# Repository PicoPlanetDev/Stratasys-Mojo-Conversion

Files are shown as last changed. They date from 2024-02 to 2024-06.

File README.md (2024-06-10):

# Stratasys Mojo Retrofit

Stratasys has ended support for their Mojo 3D printers, and you can no longer purchase parts or filament for them.
This project aims to retrofit them with off-the-shelf parts to extend their lifespan.

## Parts

Here is an example parts list that may be used for this conversion. This assumes that you repurpose the
old printer's ATX power supply and CoreXY mechanics. Minmimal irreversible changes are made to the machine,
although that doesn't really matter at this point!

I converted two printers at once for $300, a slight cost savings due to higher quantity of GT2 pulleys resulting in a lower individual price, as well as the endstops comkng in packages of six.

| **Item** | **URL** | **Price** | **Quantity** | **Total Cost** |
|:---:|:---:|:---:|:---:|:---:|
| Chimera hotend | <https://www.amazon.com/dp/B08BKMM1R7/> | $20 | 1 | $20 |
| Extruder | <https://www.amazon.com/dp/B0BZD8JMPR/> | $9 | 2 | $18 |
| Control board | <https://www.amazon.com/dp/B08PCX6TM7/> | $42 | 1 | $42 |
| Endstops | <https://www.amazon.com/dp/B07PCN6T6F/> | $11 | 1 | $11 |
| PTFE tubing | <https://www.amazon.com/dp/B01CUPV90M/> | $8 | 1 | $8 |
| Stepper motors | <https://www.amazon.com/dp/B0817TS61F/> | $38 | 1 | $38 |
| LCD display | <https://www.amazon.com/dp/B08HLSCHVL/> | $12 | 1 | $12 |
| GT2 timing belt pulleys | <https://www.amazon.com/dp/B07BT6N12L/> | $8 | 1 | $8 |
| 4010 fan | <https://www.amazon.com/dp/B0B1N6NSGM/> | $9 | 1 | $9 |
| **Total** | | | | **$166** |

You'll also need some assorted M3 screws. I use them standard across all of my designs now and just bought a little box of a few size off of Amazon. Your local hardware store might be better though!

### 3D Printed Parts

In the `cad/` subdirectory, I have included designs in both Fusion 360 and STEP formats for you to customize and export. STLs and potentially Printables links coming soon!

| **Part** | **Quantity** |
|:---:|:---:|
| Chimera Mount | 1 |
| Left Extruder Mount  | 1 |
| Right Extruder Mount | 1 |
| Stepper Mount | 3 |
| ~~Z Endstop Mount~~  | ~~1~~ |

Note that the Z Endstop Mount design is currently **not** suitable for the conversion. It doesn't allow the bed to move up enough to reach the hotend. Future revision will correct this, however,
I just use hot glue and software offsets in the meantime.

#### Buildplate

[@mebillica](https://github.com/mebillica) has improved the accuracy of my build plate design used in the PrusaSlicer model preview to the point that it can be printed and used in the abscence
of OEM buildplates, an increasingly prevalent issue with Stratasys Mojo machines after their discontinuation.

[Here's a link](https://www.thingiverse.com/thing:6648382) to his model on Thingiverse, which also includes the Fusion source if you need to make further modifications. The Fusion design and STL file
are also mirrored in this repo, in the `cad/Fusion/Build Plate` and `PrusaSlicer/buildplate` directories, respectively. If you'd prefer the Printables download, that is [available as well](https://www.printables.com/model/901716-stratasys-mojo-build-plate).

Stratasys OEM buildplates are made of some some sort of ABS plastic so that their ABS filament fuses to them. This makes them non-reuseable unless you cover first with transfer tape (and a glue stick).
However, if you're looking to print PLA using a machine retrofitted according to this guide, you may have success printing these plates out of other materials.

PrusaSlicer should now show this new buildplate design in the Plater tab when setting up your prints, giving you an even better idea of where your model lands relative to the 5" grid as well
as locking mechanism.

### Laser Cut Parts

If you have access to a laser cutter, it can be really useful for quickly making the following parts out of acrylic:

- LCD frontplate
- LCD backplate
- Control board backplate
- Control board standoffs
- Control board fan mount

However, a laser cutter is not required and these could easily be made manually with careful marking, a drill press, and a jigsaw, or 3D printed if you're willing to run a relatively long print.

These design files are not yet included.

## Assembly

### Removing original hardware

I'd suggest using a drill with the clutch limited to about 5 (attached to an appropriately sized socket head) to remove all of the screws. Probably you'll want a magnetic screw dish as well.

1. Remove the metal backplate after unscrewing all of the screws marked in red image **red** in the below image
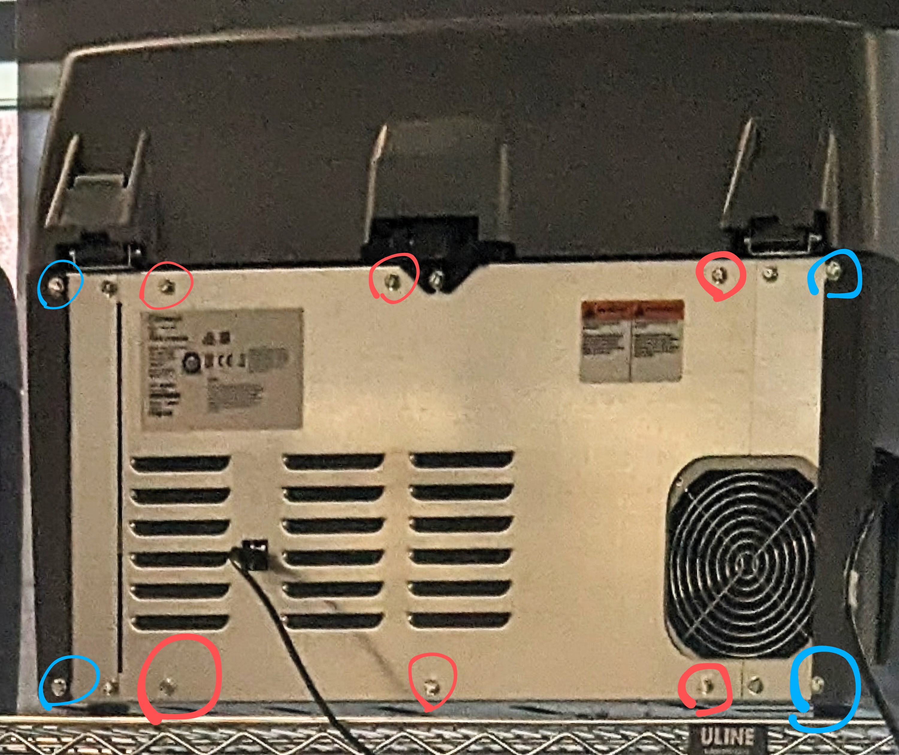
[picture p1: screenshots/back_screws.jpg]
Back screws to remove

1. Remove the two side panels after unscrewing all of the screws marked in blue image **blue** in the above image
2. Unplug every connector from the original I/O board, including the power cables and all ribbon cables
3. Unscrew each screw keeping the I/O board in place, then remove it
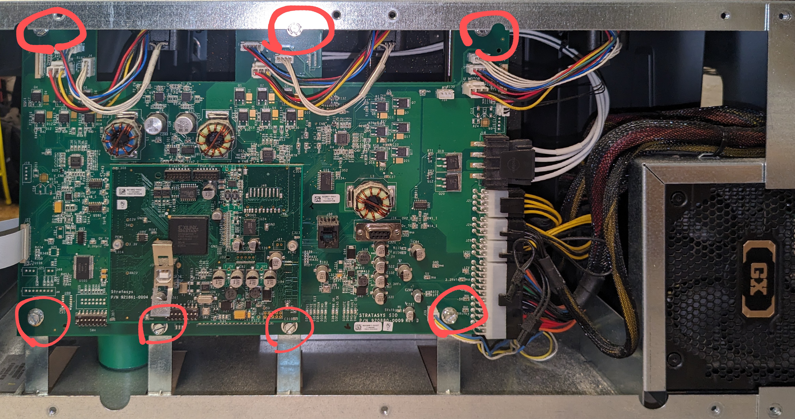
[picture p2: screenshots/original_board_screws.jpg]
I/O board screws to remove

1. *Carefully* bend the metal tabs previously holding the I/o board in place out of the way. Ideally all should be in a flush position, save for the small bump where they are attached.
2. Unscrew and remove both filament buckets. There's four obvious screws on the top, but also one hidden one that I had to use a screwdriver plus shaft extension on:
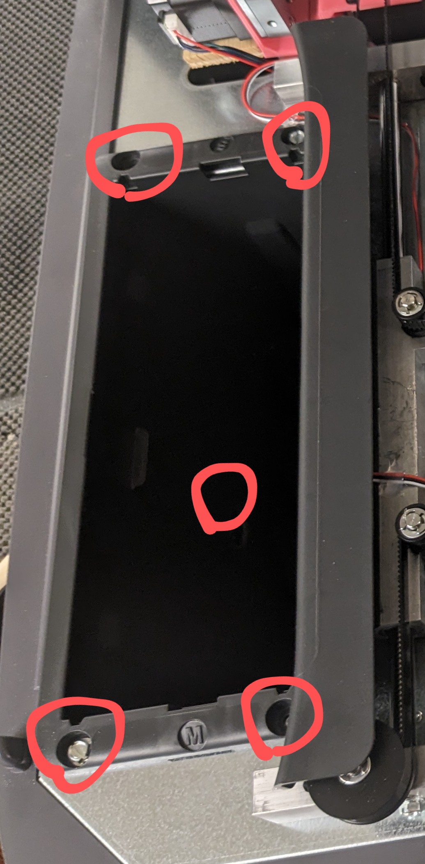
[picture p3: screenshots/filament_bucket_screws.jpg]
Filament bucket screws to remove

1. Remove the original hotend carrier. This takes some work, and many screws that I don't (yet) have documentation photos for. This is a general guide and it took at least an hour of messing with it the first time I did it.
   1. First, try unscrewing the PCB on the back
   2. Remove the belts from their tensioning system and unscrew the back from its slider
   3. Remove the clip holding the front on, and I think you can take out the entire assembly
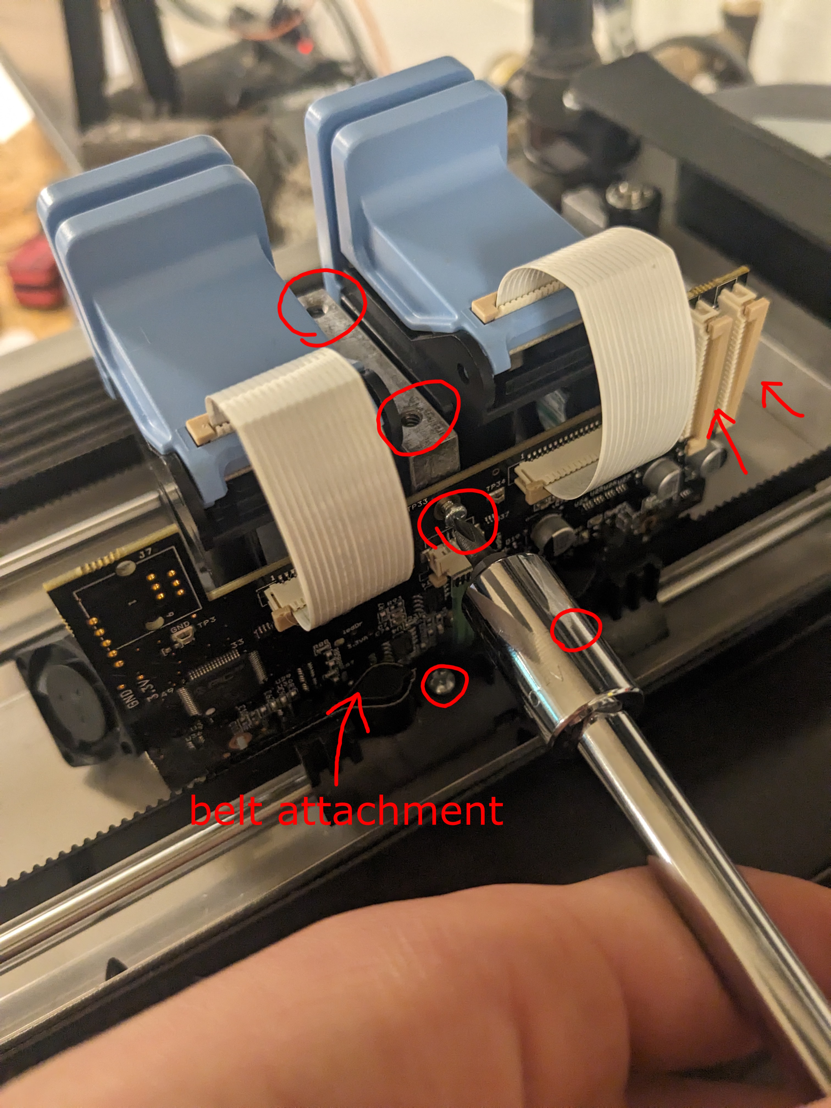
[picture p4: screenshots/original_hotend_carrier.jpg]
Hotend carrier


### Installing new hardware

In lieu of a full assembly guide (right now), I'll just add some notes.

- If you're not using a heated bed, just power the control board off of the power supply's PCIe power
  - Snip off the last couple of inches of the header
  - Twist together the three yellow wires, then separately twist together the three black wires
  - Maybe put a blob of solder on the twists to keep them in place while inserting into the control board's screw terminals
- When viewing the printer **from the back**, the left motor should be plugged into the **X** connector and the right motor into the **Y** connector
- You'll need to drill some ~1" holes through the side panels and filament buckets to accomodate a dowel rod for the filament spool
  - Alternatively, for a no-damage installation, print first one of the filament spool holder designs that uses bearings and rollers to support the filament and allow it to spin freely
- Your Y axis endstop should be on the right side when viewed **from the front** or left side when viewed **from the back**, a couple of inches towards the back away from the front block. You can identify the right position by pushing the Y axis all the way forward, then placing the endstop in a position so it is well depressed.
  - Depending on your printer, you may be able to screw down one or both of the endstop's mounting holes. I used a 1/8" drill bit and, after marking the position, drilled through the metal with a shop vac for cleanup only
- All endstops need some insulation on the bottom to prevent shorts. Either heatshrink the whole thing, which would hide the LED :(, or, as I did, liberally apply hot glue to the bottom
  - Then, for all of the endstops, use more hot glue to affix in place as necessary
- The Z axis endstop now has a custom mount consisting of a U-shaped bracket that slides over the Z axis block and a separate plate that the endstop mounts to and slides up and down on to adjust the zero offset. The U-shaped bracket probably should be glued down once everything's all set
- Don't forget that ATX computer power supplies require their PS_On pin (#6 on a 24-pin connector) to be jumped to ground to activate them. As I have not implemented power supply control, please use a short piece of wire to connect PS_on (also denoted by the green wire) to any black ground wire.

## Firmware

The firmware for the prototype single extruder system is based on Marlin 2.0.9.7 LTS which is not recommended for use with "modern" boards. For that machine, I was reusing an old mega2560 MKS Base v1.4 control board, but I could have used a newer Marlin version, and I'd suggest you update the config to do that.

The dual nozzle version is currently based on Marlin 2.1-bugfix as of 5 April 2024, but I intend to upgrade it to 2.1.3 when that becomes available. I'm using the MKS Eagle (basically Robin Nano with builtin drivers) for the production version, so the config files and binary reflect that.

### Build and Upload

As this was my first time dealing with a 32-bit control board, the process for uploading firmware was initially foreign to me. *Here's the process I found to be best for quick iteration:*

1. Clone or download [makerbase-mks/MKS-EAGLE](https://github.com/makerbase-mks/MKS-EAGLE)
2. Clone or download this repository (for easy access to the Marlin configuration files)
3. Download and extract the appropriate version of Marlin from [this page](https://marlinfw.org/meta/download/)
4. Copy the configuration files from the appropriate subfolder of the `firmware` folder in this repository, and paste them in the Marlin subfolder that you extracted. You should see in the same directory the folders `lib` and `src` in addition to the file `Marlin.ino` if you're in the right place.
5. Install [Visual Studio Code](https://code.visualstudio.com/#alt-downloads) using the download link for your platform
6. Set up Auto Build Marlin according to [these instructions](https://marlinfw.org/docs/basics/auto_build_marlin.html)
7. Customize the example configuration
8. Build using the Build button in the Auto Build Marlin window
9. Find your `mks_eagle.bin` output file. It should be located in `../.pio' folder (one level outside of the Marlin folder)
10. Copy `mks_eagle.bin` to the `DFU-upload` folder downloaded from the MKS-EAGLE repository. Overwrite the `mks_eagle.bin` that's already there.
11. Ensure that your control board is entirely unpowered, then move the board's power jumper (near the USB Type B port and microSD slot) to USB power (on)
12. Press and hold the `BOOT0` button on the board, then plug it in to your computer using the included cable. Once it's plugged in, release the button.
13. Download and run the latest version of [Zadig](https://zadig.akeo.ie/), which will help install necessary USB drivers.
14. Once Zadig is running, click `Options` then `List All Devices` then select from the top dropdown a device like `STM Bootloader`
15. Set the driver in the right-side combobox to WinUSB, and then click `Replace Driver`. This process can surprisingly take a few minutes to complete.
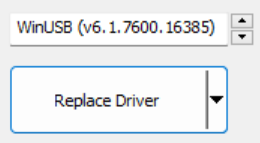
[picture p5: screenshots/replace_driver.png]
Screenshot of Zadig window for driver replacement

16. In the `MKS-EAGLE/DFU-upload` folder, run `DFU-Upload-firmware.bat`
17. Once flashing is complete, unplug the board and change the power jumper back to off (so no USB power)
18. Turn on your power supply and test the firmware!

## Slicer

I selected PrusaSlicer for its robustness and ease of customization, however, I believe that derivatives such as SuperSlicer or OrcaSlicer will also work.
Or, if you prefer Cura, as I do for my other machines, the configuration should be easy enough to replicate.

1. Install [PrusaSlicer](https://www.prusa3d.com/en/page/prusaslicer_424/).
2. Copy the PrusaSlicer folder from this repository
3. Navigate to `C:/Users/YOUR_USERNAME/AppData/Roaming` in your file explorer. You can do this easily by typing in the directory bar `%APPDATA%` and pressing <kbd>Enter</kbd>.
4. Paste the PrusaSlicer folder, and select *Replace the file in the destination* if prompted. This will install the  filament settings, print settings, and printer settings I have tuned for the Stratasys Mojo conversion.
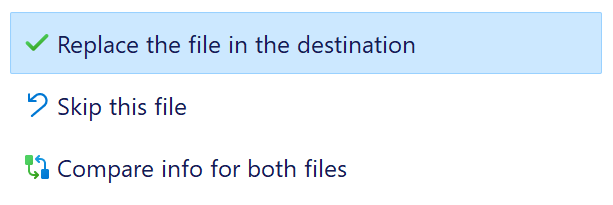
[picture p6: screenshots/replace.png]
Replace file dialog

5. Open PrusaSlicer and navigate to *Printer Settings*.
6. Ensure that Expert mode is selected by pressing the button in the top right.
7. Navigate to *General* > *Bed Shape*.
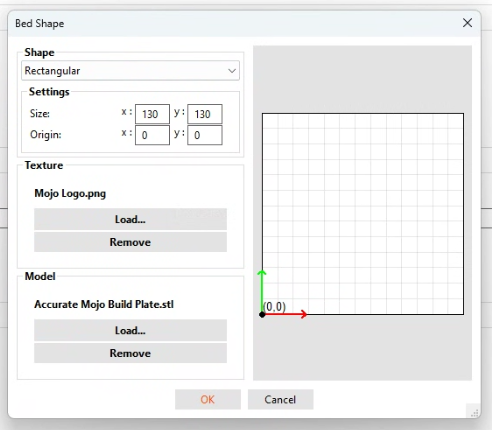
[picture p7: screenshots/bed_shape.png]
Bed Shape dialog

1. Load the `Mojo Logo.png` file from the `PrusaSlicer/buildplate` folder you copied as the bed texture.
2. Load the `Accurate Mojo Build Plate.stl` file `PrusaSlicer/buildplate` folder you copied as the bed model.

## Usage Instructions

I created a guide with instructions for a novice user to prepare a model for printing on one of these converted machines.
That document is available here: [Stratasys Mojo Instructions](https://docs.google.com/document/d/1dcEKFhcxA-QaMBZmRmVCBlgQjbNByx9ydnzFRXKonwo/edit?usp=sharing)

## TODO

- [x] Update to 2.1-bugfix
- [x] Implement M16 in print profile to ensure that the right profile (dual vs single extruder) was used
- [ ] ~~Figure out feasibility of ATX power supply enable / disable and standby power~~
- [ ] Consider MPC temperature instead of PID
- [ ] Consider S-Curve acceleration
- [ ] Consider nozzle clean
- [ ] Enable linear advance
- [ ] ~~Consider sensorless homing~~
- [ ] Create X axis endstop mount
- [x] Create both extruder mounts

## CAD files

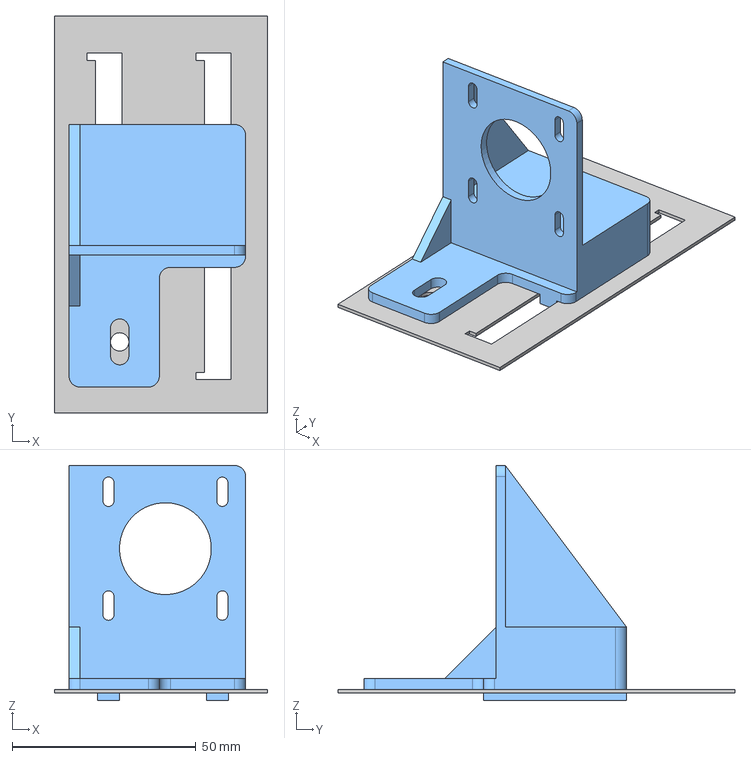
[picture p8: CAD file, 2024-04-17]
cad/STEP/Right Extruder Mount v5.step
58.1 x 108.0 x 64.0 mm
Metal Base
Mounting Plate

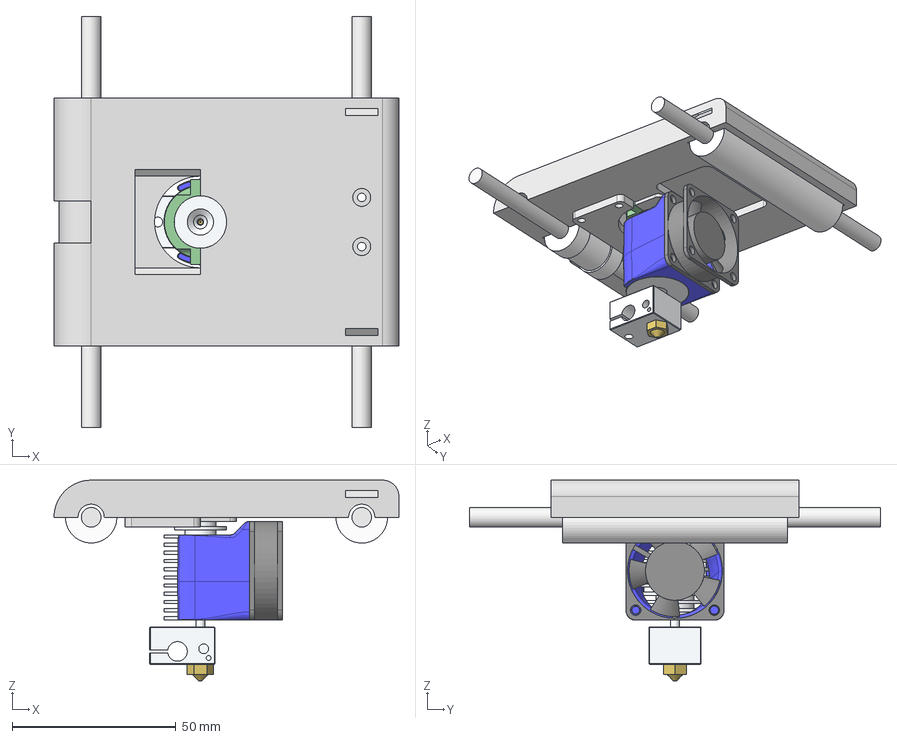
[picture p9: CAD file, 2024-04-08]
cad/STEP/Single Nozzle/Hotend Mount v22.step
105.3 x 125.5 x 61.3 mm
e3d nozzle (0.4)
e3d heaterblock
e3d heat break
e3d heatsink
fan duct
fan sub1
fan sub2
Back Rail
Front Rail
Front Slider
Back Slider
Hotend Carrier
Hotend Clamp
Bottom Cover Panel

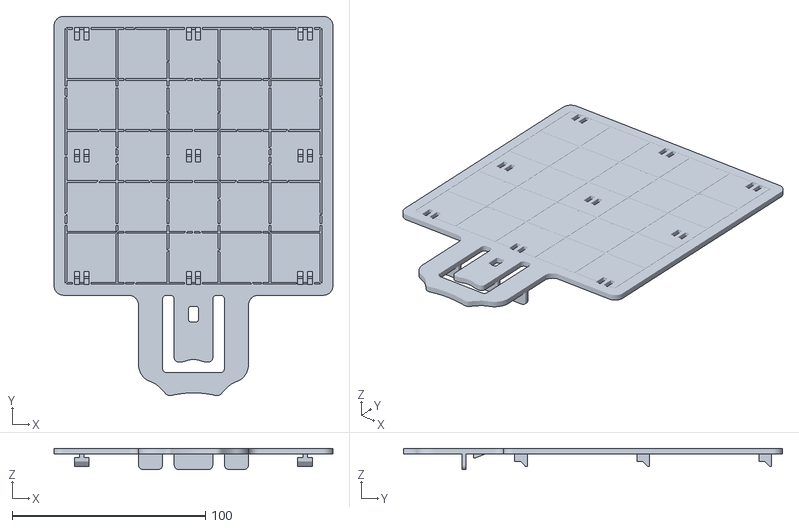
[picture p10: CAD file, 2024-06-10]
PrusaSlicer/buildplate/Accurate Mojo Build Plate.stl
144.5 x 196.5 x 11.0

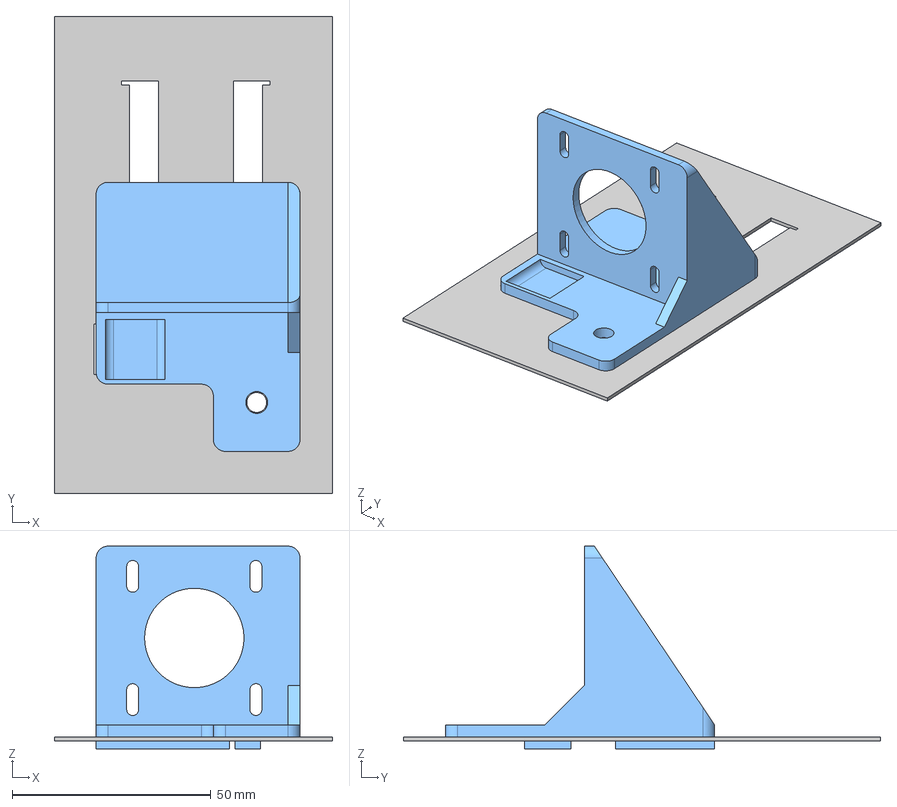
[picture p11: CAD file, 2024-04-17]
cad/STEP/Left Extruder Mount v14.step
70.0 x 120.0 x 51.0 mm
Metal Panel (Left)
Mount Plate

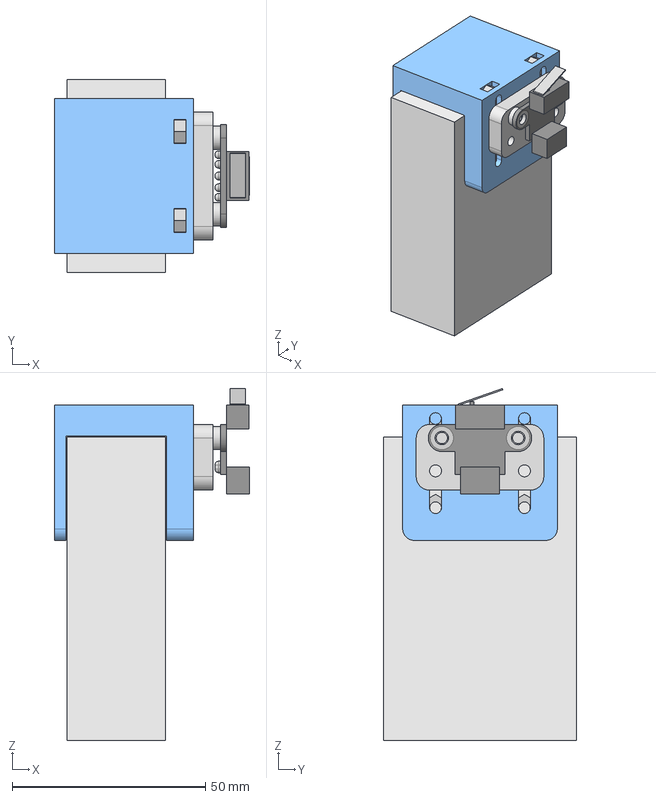
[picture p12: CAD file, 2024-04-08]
cad/STEP/Z Endstop Mount v9.step
50.5 x 50.0 x 91.1 mm
Endstop_1
Build Plate Carrier Block
Carrier Block Clip
Endstop Slider
M3 Nut x 4

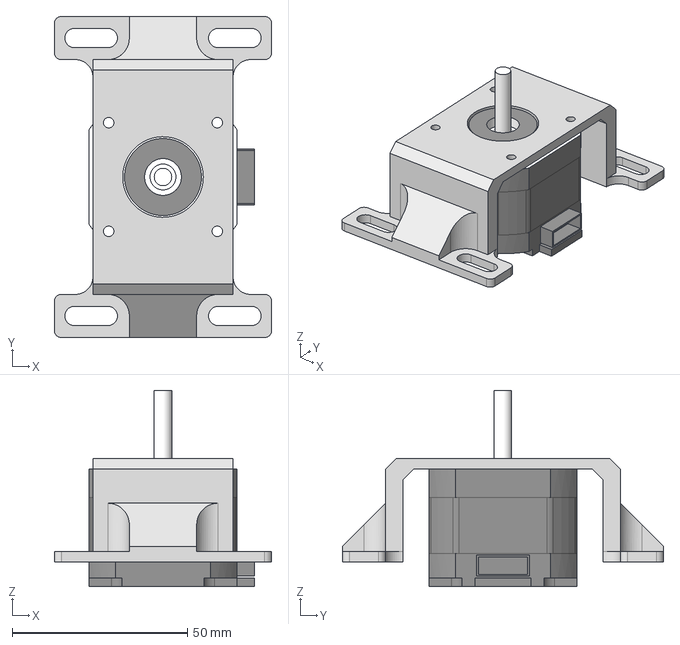
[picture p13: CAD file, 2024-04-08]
cad/STEP/Stepper Mount v8.step
62.0 x 91.6 x 56.0 mm
Nema 17
Stepper Mount_1

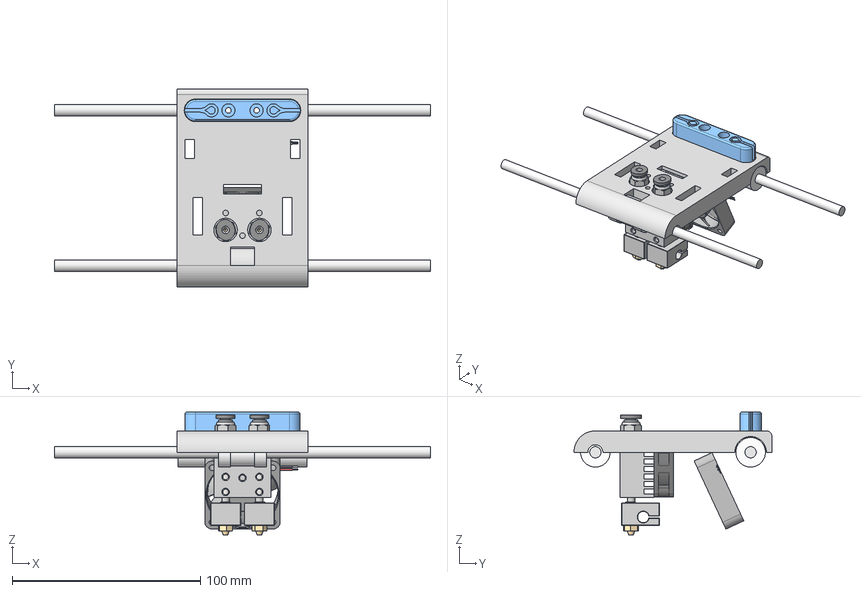
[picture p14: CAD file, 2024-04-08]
cad/STEP/Chimera Mount v20.step
200.0 x 105.3 x 65.3 mm
Back Rail
Front Rail
Back Slider
Front Slider
Heat Sink
Brass Nozzle x 2
V6 Heat Block x 2
V6 Hotend Barrel x 2
Push Fitting x 2
40x40x10 DC Fan
Chimera Carrier
Belt Attachment

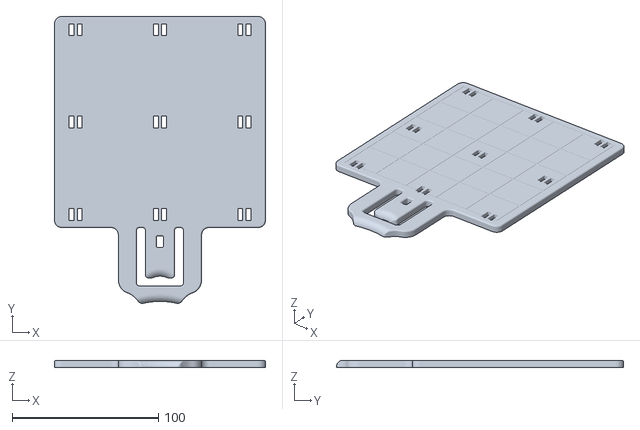
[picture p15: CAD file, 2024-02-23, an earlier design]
PrusaSlicer/buildplate/Old Buildplate.stl
144.5 x 196.5 x 5.00

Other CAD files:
cad/Fusion/Build Plate/Mojo Build Plate v5.f3d
cad/Fusion/Chimera Mount v20.f3z
cad/Fusion/Left Extruder Mount v14.f3z
cad/Fusion/Right Extruder Mount v5.f3z
cad/Fusion/Single Nozzle/Extruder Mount v8.f3z
cad/Fusion/Single Nozzle/Hotend Mount v22.f3d
cad/Fusion/Stepper Mount v8.f3z
cad/Fusion/Z Endstop Mount v9.f3z

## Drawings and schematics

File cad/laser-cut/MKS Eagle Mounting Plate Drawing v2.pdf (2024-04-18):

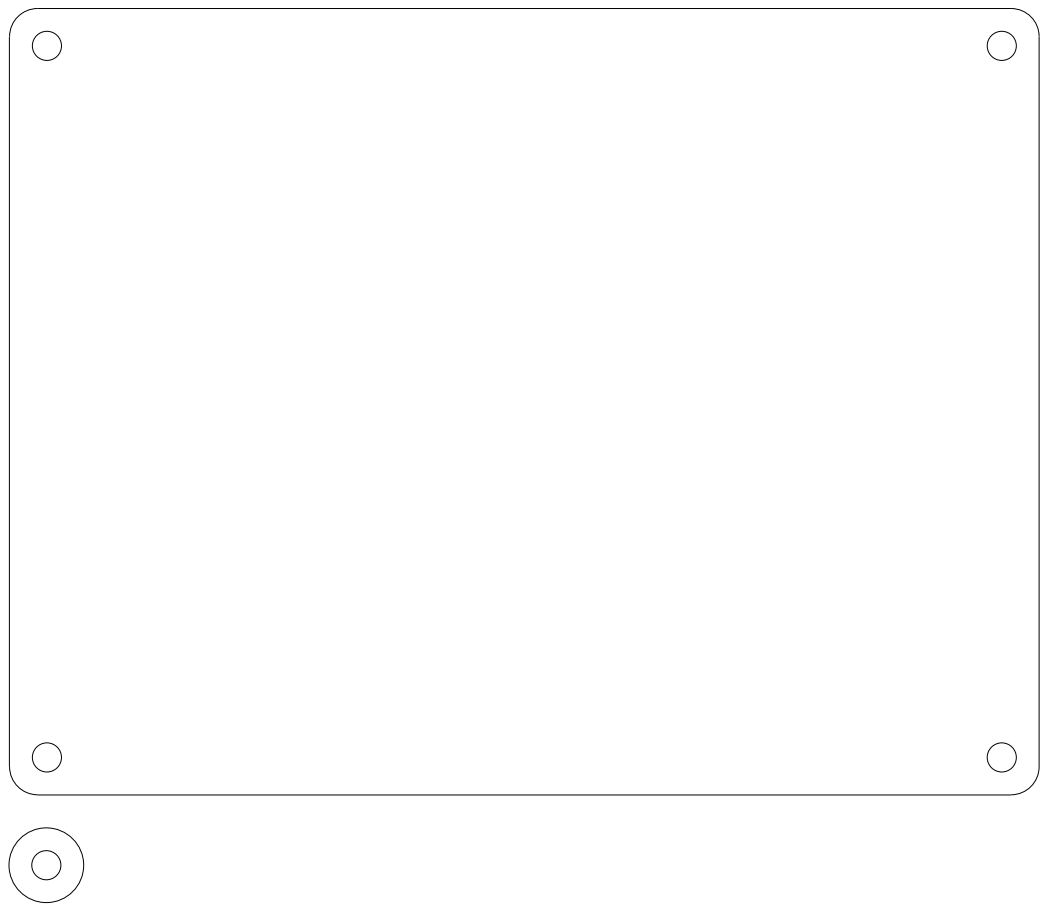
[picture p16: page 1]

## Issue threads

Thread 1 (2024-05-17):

Great project, but I have a side question

mebillica, 2024-05-17:
This project looks very interesting. I recently acquired a MOJO from work. I have a bunch of filament, but only 1 build plate. Do you happen to have the build plate in fusion360? I would like to print out more on my other printers. Thanks for any help, and keep up the good work with this!!

Bill

PicoPlanetDev, 2024-05-17:
Hi Bill!

Thanks for your interest in this project -- we actually had the opposite
problem, too many build plates and only a little filament left (the basis
for this project). I do have the build plate in Fusion and I'll send it to
you when I get a chance later today, however I don't think it has the
little locking tabs on the bottom. I'll try and add that to my design, but
I mainly had that design for the PrusaSlicer visualization only.
Here's what we do to conserve build plates though, as it may help you out.
Get some really wide blue painter's tape, or less expensive transfer tape,
and cover the build plate. Then, cut the excess off the edges and use a
plastic squeegee or scraper to flatten out air bubbles. Finally, use a glue
stick to make it sticky. In that way we get many uses out of the same build
plate by just re-covering it each time.

I'll update you on the file when I have a chance.

Best,
Sig

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

PicoPlanetDev, 2024-05-20:
@mebillica Just uploaded the Fusion design file for it. However, this version is pretty much for aesthetics only and I don't guarantee it's entirely true to life. It also lacks those clips. I can work on it a little more later to try and get a usable printable version.
https://github.com/PicoPlanetDev/Stratasys-Mojo-Conversion/blob/main/cad/Fusion/Mojo%20Build%20Plate%20v5.f3d

mebillica, 2024-05-21:
Thank you so much!! Wow, I'll be printing this tonight when I get home! Maybe I can figure out the tabs. Not the best in Fusion. I did see another video, where someone put down a little glue stick, all over the plate, then covered it completely with Kapton tape. This worked EXTREMELY well! So at least I have it protected.

mebillica, 2024-05-31:
Am update for you. My Fusion360 skills are not the best, but I have the tabs added, and the little "lock" as well. I've printed this in ABS on my home Prusa MK4. They fit PERFECTLY onto the Mojo! Snaps/locks in perfect! I have printed on them. They work just like the original build plates. I have read the original plates are ABS as well, but I don't know. MY plates will melt/warp in the wash station. Stock plate does not. But I have found that Kapton/glue stick trick works AMAZINGLY well! When the print finishes, give a little twist to the plate, and the part pops off! Larger, 3x3 print, showed a minor corners lifting. So I'm thinking anything bigger than 3x3 will require a plate without the Kapton tape. But now that I can print plates at home, that doesn't matter. You saved me big time, as I only had the single plate! Would you mind if I uploaded the STL to thingiverse? Might help someone else in need. I'll attach the files here later from my PC for you. Thanks again!!

Bill
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

PicoPlanetDev, 2024-05-31:
These build plates look great! I'd love if you were able to upload the STL to Thingiverse, as I'm sure one day many labs like ours will run out. Whenever you get the chance to share the Fusion files as well, I'll update that in this repo / or make a pull request for it.

I'm glad the transfer tape solution has been working out, as it's really saved us for many prints. With regards to the warping, I have found that to be the case sometimes as well. Not sure if you can get around it too much but we do have discussions of whether we should "burn a plate" for a critical print or if we can just do it with the tape.

I've actually never put the build plates in the wash bath! We always use a long old flat head screwdriver to chip the raft off of the bottom, and clean off as much support as possible so we don't use up our wash bath chemical too fast. Maybe that'll help in the reuse of those plates. I wonder, if that solution does work out, if they could even be printed in PLA and not melt too badly as it prints.

All in all, your design looks great though and this is a huge contribution to the project and community (if there is one) surrounding these old machines.

mebillica, 2024-06-03:
OK. github wont let me upload the file. says file type not supported. So I think I have it uploaded to my Google Drive. Here's the link.

 [](https://drive.google.com/drive/folders/1Ic4q2AD9QrNfCmKSSI06L3VmGddkp6xw?usp=drive_link)

Let me know if you got the f3d and stl ok. If not, I could email them to you.

Bill

mebillica, 2024-06-10:
OK, I added the Build plate to Thingiverse. Here's the link:

https://www.thingiverse.com/thing:6648382

Thanks again!

Bill

PicoPlanetDev, 2024-06-10:
These files are great and I'll drop them into the repository in a bit. Thanks so much for this contribution to keeping these machines alive!

PicoPlanetDev, 2024-06-10:
Pull request #2 brings these changes onto the main branch. Let me know if there's anything else I can help with!

Closed 2024-06-10.

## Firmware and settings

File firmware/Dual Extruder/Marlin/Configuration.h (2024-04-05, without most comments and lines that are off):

#pragma once
#define CONFIGURATION_H_VERSION 02010300
#define STRING_CONFIG_H_AUTHOR "Sigmond Kukla" // Who made the changes.
  #define MOTHERBOARD BOARD_MKS_EAGLE
#define SERIAL_PORT -1
#define BAUDRATE 250000
#define CUSTOM_MACHINE_NAME "Stratasys Mojo Dual Nozzle"
#define X_DRIVER_TYPE  TMC2209
#define Y_DRIVER_TYPE  TMC2209
#define Z_DRIVER_TYPE  TMC2209
#define E0_DRIVER_TYPE TMC2209
#define E1_DRIVER_TYPE TMC2209
#define EXTRUDERS 2
#define DEFAULT_NOMINAL_FILAMENT_DIA 1.75
#define HOTEND_OFFSET_X { 0.0, 18.00 } // (mm) relative X-offset for each nozzle
#define HOTEND_OFFSET_Y { 0.0, 0.00 }  // (mm) relative Y-offset for each nozzle
#define HOTEND_OFFSET_Z { 0.0, 0.00 }  // (mm) relative Z-offset for each nozzle
#define TEMP_SENSOR_0 1
#define TEMP_SENSOR_1 1
#define TEMP_SENSOR_2 0
#define TEMP_SENSOR_3 0
#define TEMP_SENSOR_4 0
#define TEMP_SENSOR_5 0
#define TEMP_SENSOR_6 0
#define TEMP_SENSOR_7 0
#define TEMP_SENSOR_BED 0
#define TEMP_SENSOR_PROBE 0
#define TEMP_SENSOR_CHAMBER 0
#define TEMP_SENSOR_COOLER 0
#define TEMP_SENSOR_BOARD 0
#define TEMP_SENSOR_SOC 0
#define TEMP_SENSOR_REDUNDANT 0
#define DUMMY_THERMISTOR_998_VALUE  25
#define DUMMY_THERMISTOR_999_VALUE 100
#if TEMP_SENSOR_IS_MAX_TC(0)
  #define MAX31865_SENSOR_OHMS_0      100 // (Ω) Typically 100 or 1000 (PT100 or PT1000)
  #define MAX31865_CALIBRATION_OHMS_0 430 // (Ω) Typically 430 for Adafruit PT100; 4300 for Adafruit PT1000
#endif
#if TEMP_SENSOR_IS_MAX_TC(1)
  #define MAX31865_SENSOR_OHMS_1      100
  #define MAX31865_CALIBRATION_OHMS_1 430
#endif
#if TEMP_SENSOR_IS_MAX_TC(2)
  #define MAX31865_SENSOR_OHMS_2      100
  #define MAX31865_CALIBRATION_OHMS_2 430
#endif
#if HAS_E_TEMP_SENSOR
  #define TEMP_RESIDENCY_TIME         10  // (seconds) Time to wait for hotend to "settle" in M109
  #define TEMP_WINDOW                  1  // (°C) Temperature proximity for the "temperature reached" timer
  #define TEMP_HYSTERESIS              3  // (°C) Temperature proximity considered "close enough" to the target
#endif
#if TEMP_SENSOR_BED
  #define TEMP_BED_RESIDENCY_TIME     10  // (seconds) Time to wait for bed to "settle" in M190
  #define TEMP_BED_WINDOW              1  // (°C) Temperature proximity for the "temperature reached" timer
  #define TEMP_BED_HYSTERESIS          3  // (°C) Temperature proximity considered "close enough" to the target
#endif
#if TEMP_SENSOR_CHAMBER
  #define TEMP_CHAMBER_RESIDENCY_TIME 10  // (seconds) Time to wait for chamber to "settle" in M191
  #define TEMP_CHAMBER_WINDOW          1  // (°C) Temperature proximity for the "temperature reached" timer
  #define TEMP_CHAMBER_HYSTERESIS      3  // (°C) Temperature proximity considered "close enough" to the target
#endif
#if TEMP_SENSOR_REDUNDANT
  #define TEMP_SENSOR_REDUNDANT_SOURCE    E1  // The sensor that will provide the redundant reading.
  #define TEMP_SENSOR_REDUNDANT_TARGET    E0  // The sensor that we are providing a redundant reading for.
  #define TEMP_SENSOR_REDUNDANT_MAX_DIFF  10  // (°C) Temperature difference that will trigger a print abort.
#endif
#define HEATER_0_MINTEMP   5
#define HEATER_1_MINTEMP   5
#define HEATER_2_MINTEMP   5
#define HEATER_3_MINTEMP   5
#define HEATER_4_MINTEMP   5
#define HEATER_5_MINTEMP   5
#define HEATER_6_MINTEMP   5
#define HEATER_7_MINTEMP   5
#define BED_MINTEMP        5
#define CHAMBER_MINTEMP    5
#define HEATER_0_MAXTEMP 275
#define HEATER_1_MAXTEMP 275
#define HEATER_2_MAXTEMP 275
#define HEATER_3_MAXTEMP 275
#define HEATER_4_MAXTEMP 275
#define HEATER_5_MAXTEMP 275
#define HEATER_6_MAXTEMP 275
#define HEATER_7_MAXTEMP 275
#define BED_MAXTEMP      150
#define CHAMBER_MAXTEMP  60
#define HOTEND_OVERSHOOT 15   // (°C) Forbid temperatures over MAXTEMP - OVERSHOOT
#define BED_OVERSHOOT    10   // (°C) Forbid temperatures over MAXTEMP - OVERSHOOT
#define COOLER_OVERSHOOT  2   // (°C) Forbid temperatures closer than OVERSHOOT
#define PIDTEMP           // See the PID Tuning Guide at https://reprap.org/wiki/PID_Tuning
#define PID_MAX  255      // Limit hotend current while PID is active (see PID_FUNCTIONAL_RANGE below); 255=full current
#define PID_K1     0.95   // Smoothing factor within any PID loop
    #define DEFAULT_Kp  22.20
    #define DEFAULT_Ki   1.08
    #define DEFAULT_Kd 114.00
#define MAX_BED_POWER 255 // limits duty cycle to bed; 255=full current
#define MAX_CHAMBER_POWER 255 // limits duty cycle to chamber heater; 255=full current
  #define PID_FUNCTIONAL_RANGE 10 // If the temperature difference between the target temperature and the actual temperature
#define PREVENT_COLD_EXTRUSION
#define EXTRUDE_MINTEMP 170
#define PREVENT_LENGTHY_EXTRUDE
#define EXTRUDE_MAXLENGTH 1000
#define THERMAL_PROTECTION_HOTENDS // Enable thermal protection for all extruders
#define THERMAL_PROTECTION_BED     // Enable thermal protection for the heated bed
#define THERMAL_PROTECTION_CHAMBER // Enable thermal protection for the heated chamber
#define THERMAL_PROTECTION_COOLER  // Enable thermal protection for the laser cooling
#define COREXY
#define ENDSTOPPULLUPS
#define X_MIN_ENDSTOP_HIT_STATE HIGH
#define X_MAX_ENDSTOP_HIT_STATE HIGH
#define Y_MIN_ENDSTOP_HIT_STATE HIGH
#define Y_MAX_ENDSTOP_HIT_STATE HIGH
#define Z_MIN_ENDSTOP_HIT_STATE HIGH
#define Z_MAX_ENDSTOP_HIT_STATE HIGH
#define I_MIN_ENDSTOP_HIT_STATE HIGH
#define I_MAX_ENDSTOP_HIT_STATE HIGH
#define J_MIN_ENDSTOP_HIT_STATE HIGH
#define J_MAX_ENDSTOP_HIT_STATE HIGH
#define K_MIN_ENDSTOP_HIT_STATE HIGH
#define K_MAX_ENDSTOP_HIT_STATE HIGH
#define U_MIN_ENDSTOP_HIT_STATE HIGH
#define U_MAX_ENDSTOP_HIT_STATE HIGH
#define V_MIN_ENDSTOP_HIT_STATE HIGH
#define V_MAX_ENDSTOP_HIT_STATE HIGH
#define W_MIN_ENDSTOP_HIT_STATE HIGH
#define W_MAX_ENDSTOP_HIT_STATE HIGH
#define Z_MIN_PROBE_ENDSTOP_HIT_STATE HIGH
#define DEFAULT_AXIS_STEPS_PER_UNIT   { 80, 80, 3080, 100.64 }
#define EDITABLE_STEPS_PER_UNIT
#define DEFAULT_MAX_FEEDRATE          { 300, 300, 5, 25 }
#define DEFAULT_MAX_ACCELERATION      { 2000, 2000, 100, 10000 }
#define DEFAULT_ACCELERATION          2000    // X, Y, Z and E acceleration for printing moves
#define DEFAULT_RETRACT_ACCELERATION  3000    // E acceleration for retracts
#define DEFAULT_TRAVEL_ACCELERATION   2000    // X, Y, Z acceleration for travel (non printing) moves
  #define JUNCTION_DEVIATION_MM 0.013 // (mm) Distance from real junction edge
  #define JD_HANDLE_SMALL_SEGMENTS    // Use curvature estimation instead of just the junction angle
#define Z_MIN_PROBE_USES_Z_MIN_ENDSTOP_PIN
#define NOZZLE_TO_PROBE_OFFSET { 10, 10, 0 }
#define PROBING_TOOL 0
#define PROBING_MARGIN 10
#define XY_PROBE_FEEDRATE (133*60)
#define Z_PROBE_FEEDRATE_FAST (4*60)
#define Z_PROBE_FEEDRATE_SLOW (Z_PROBE_FEEDRATE_FAST / 2)
#define Z_CLEARANCE_DEPLOY_PROBE   10 // (mm) Z Clearance for Deploy/Stow
#define Z_CLEARANCE_BETWEEN_PROBES  5 // (mm) Z Clearance between probe points
#define Z_CLEARANCE_MULTI_PROBE     5 // (mm) Z Clearance between multiple probes
#define Z_PROBE_ERROR_TOLERANCE     3 // (mm) Tolerance for early trigger (<= -probe.offset.z + ZPET)
#define Z_PROBE_LOW_POINT          -2 // (mm) Farthest distance below the trigger-point to go before stopping
#define X_ENABLE_ON 0
#define Y_ENABLE_ON 0
#define Z_ENABLE_ON 0
#define E_ENABLE_ON 0 // For all extruders
#define DISABLE_OTHER_EXTRUDERS   // Keep only the active extruder enabled
#define INVERT_X_DIR true
#define INVERT_Y_DIR true
#define INVERT_Z_DIR false
#define INVERT_E0_DIR false
#define INVERT_E1_DIR false
#define INVERT_E2_DIR false
#define INVERT_E3_DIR false
#define INVERT_E4_DIR false
#define INVERT_E5_DIR false
#define INVERT_E6_DIR false
#define INVERT_E7_DIR false
#define Z_AFTER_HOMING         10   // (mm) Height to move to after homing (if Z was homed)
#define X_HOME_DIR -1
#define Y_HOME_DIR -1
#define Z_HOME_DIR -1
#define X_BED_SIZE 130
#define Y_BED_SIZE 130
#define X_MIN_POS 0
#define Y_MIN_POS 0
#define Z_MIN_POS 0
#define X_MAX_POS X_BED_SIZE
#define Y_MAX_POS Y_BED_SIZE
#define Z_MAX_POS 130
#define MIN_SOFTWARE_ENDSTOPS
  #define MIN_SOFTWARE_ENDSTOP_X
  #define MIN_SOFTWARE_ENDSTOP_Y
  #define MIN_SOFTWARE_ENDSTOP_Z
  #define MIN_SOFTWARE_ENDSTOP_I
  #define MIN_SOFTWARE_ENDSTOP_J
  #define MIN_SOFTWARE_ENDSTOP_K
  #define MIN_SOFTWARE_ENDSTOP_U
  #define MIN_SOFTWARE_ENDSTOP_V
  #define MIN_SOFTWARE_ENDSTOP_W
#define MAX_SOFTWARE_ENDSTOPS
  #define MAX_SOFTWARE_ENDSTOP_X
  #define MAX_SOFTWARE_ENDSTOP_Y
  #define MAX_SOFTWARE_ENDSTOP_Z
  #define MAX_SOFTWARE_ENDSTOP_I
  #define MAX_SOFTWARE_ENDSTOP_J
  #define MAX_SOFTWARE_ENDSTOP_K
  #define MAX_SOFTWARE_ENDSTOP_U
  #define MAX_SOFTWARE_ENDSTOP_V
  #define MAX_SOFTWARE_ENDSTOP_W
#define HOMING_FEEDRATE_MM_M { (50*60), (50*60), (4*60) }
#define VALIDATE_HOMING_ENDSTOPS
#define EEPROM_SETTINGS     // Persistent storage with M500 and M501
#define EEPROM_CHITCHAT       // Give feedback on EEPROM commands. Disable to save flash.
#define EEPROM_BOOT_SILENT    // Keep M503 quiet and only give errors during first load
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

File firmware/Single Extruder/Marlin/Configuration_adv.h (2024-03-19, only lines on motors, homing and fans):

#define E0_AUTO_FAN_PIN -1
#define E1_AUTO_FAN_PIN -1
#define E2_AUTO_FAN_PIN -1
#define E3_AUTO_FAN_PIN -1
#define E4_AUTO_FAN_PIN -1
#define E5_AUTO_FAN_PIN -1
#define E6_AUTO_FAN_PIN -1
#define E7_AUTO_FAN_PIN -1
#define CHAMBER_AUTO_FAN_PIN -1
#define COOLER_AUTO_FAN_PIN -1
#define HOMING_BUMP_MM      { 5, 5, 2 }       // (mm) Backoff from endstops after first bump
#define HOMING_BUMP_DIVISOR { 2, 2, 4 }       // Re-Bump Speed Divisor (Divides the Homing Feedrate)
#define MICROSTEP_MODES { 16, 16, 16, 16, 16, 16 } // [1,2,4,8,16]
#define ADVANCED_PAUSE_FEATURE
  #define ADVANCED_PAUSE_PURGE_FEEDRATE        3  // (mm/s) Extrude feedrate (after loading). Should be slower than load feedrate.
  #define ADVANCED_PAUSE_PURGE_LENGTH         10  // (mm) Length to extrude after loading.
  #define ADVANCED_PAUSE_RESUME_PRIME          0  // (mm) Extra distance to prime nozzle after returning from park.

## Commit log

2024-02-24 Added dual extrusion
    [Configuration.h, Configuration_adv.h]
2024-02-26 Added E3D V6 hotend mount
    [Hotend Mount v19.step]
2024-02-26 Update readme to reflect addition of hotend mount cad
2024-02-26 Add stepper mount CAD
    [Stepper Mount v4.step]
2024-03-19 Update single nozzle config from testing
    [Configuration.h, Configuration_adv.h]
2024-04-01 Update dual extruder config
    [Configuration.h, Configuration_adv.h]
2024-04-04 Update to match actual testing
    [Configuration.h]
2024-04-05 Add new config
    [Configuration.h, Configuration_adv.h]
2024-04-08 Add updated CAD models
    [Chimera Mount v20.f3z, Chimera Mount v20.step, Extruder Mount v8.f3z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]
2024-04-08 Move build plate files to buildplate folder
    [Accurate Mojo Build Plate.stl]
2024-04-09 Add assembly instructions
2024-04-09 Annotate hotend carrier screenshot
2024-04-11 Rearranged folder structure
    [Accurate Mojo Build Plate.stl, Configuration.h, Configuration_adv.h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]
2024-04-17 Add right extruder mount and update left extruder mount
    [Left Extruder Mount v12.f3z, Left Extruder Mount v14.f3z, Left Extruder Mount v14.step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]
2024-04-17 Added laser cutting notes to README
2024-04-18 Add laser cut parts
2024-05-20 Add build plate
    [Mojo Build Plate v5.f3d]
2024-06-10 Add new buildplate models from mebillica
    [Accurate Mojo Build Plate.stl, Mojo Build Plate v5.f3d, Old Buildplate.stl]
2024-06-10 Update README.md
    Reflect that extruder mounts are now available
2024-06-10 Update README.md
    Add note about ATX power supply

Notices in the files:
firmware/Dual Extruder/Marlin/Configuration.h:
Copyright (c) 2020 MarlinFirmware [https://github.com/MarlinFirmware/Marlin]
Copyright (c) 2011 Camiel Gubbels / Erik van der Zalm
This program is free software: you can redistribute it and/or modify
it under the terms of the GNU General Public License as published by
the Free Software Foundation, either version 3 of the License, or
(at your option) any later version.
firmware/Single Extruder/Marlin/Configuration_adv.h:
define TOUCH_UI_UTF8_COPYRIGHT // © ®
